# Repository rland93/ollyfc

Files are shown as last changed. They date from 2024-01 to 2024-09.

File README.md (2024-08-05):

# ollyfc
A small rust-embedded flight computer. RTIC, FrSky protocols, and STM32F4 hardware.

Board bring-up progress:

- [x] Buzzer
- [x] HDC 1080 Humidity and Temperature Sensor
- [x] BMI088 IMU
- [x] PCA9865 PWM Controller
- [x] Servo Channels from 5v power rail
- [x] FrSky SBUS External Reciever
- [x] BMP388 Pressure Sensor
- [x] LIS3MDL Magnetometer
- [x] FrSky SBUS 
- [ ] U-blox NEO m8n GPS unit
- [ ] NPA 730B differential pressure sensor
- [x] W25Q External Flash Memory
- [ ] UART for holybro 915MHz telemetry radio

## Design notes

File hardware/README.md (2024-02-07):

# OllyFC Hardware

We have hardware!

Schematics:

+ [V1 Schematic (PDF Link)](v1/ollyfc_v1_schematic.pdf)

# v1

V1 is manufactured by JLCPCB. The final project files (including JLCPCB Part Numbers / Bill of Materials) is in the v1/production folder. Images:

3D View (Tilted)

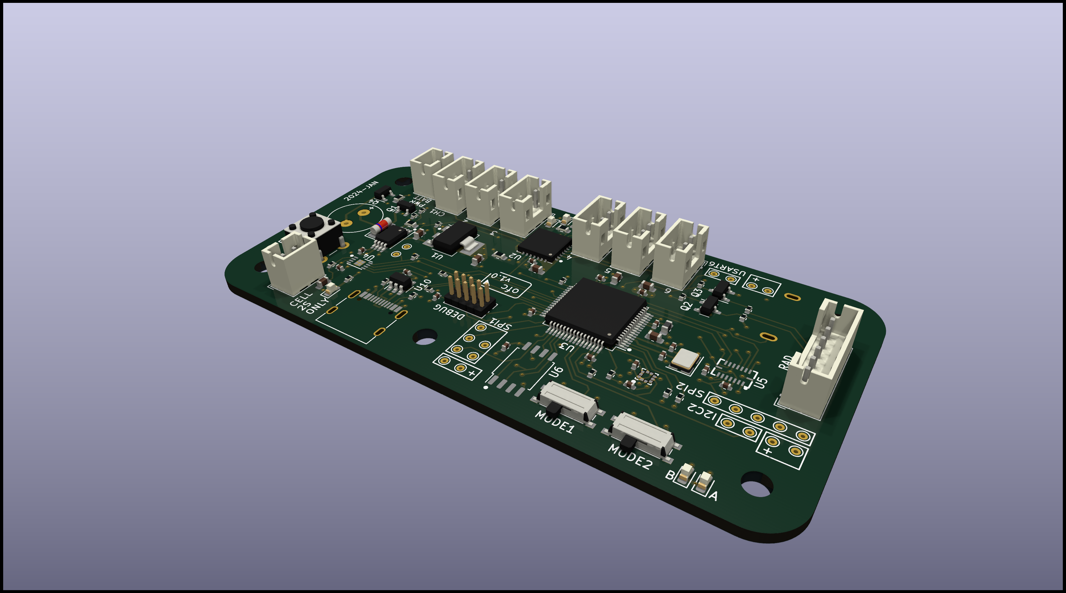
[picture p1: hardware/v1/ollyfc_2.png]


3D View (Top)

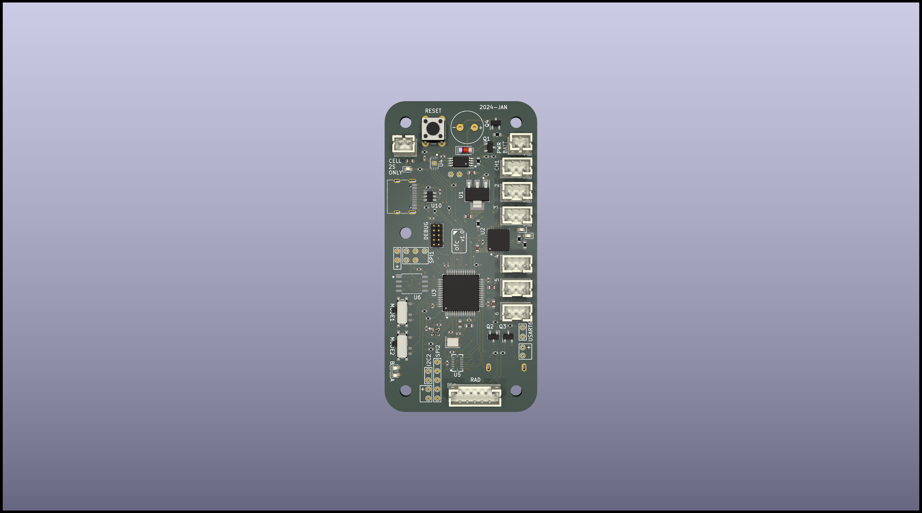
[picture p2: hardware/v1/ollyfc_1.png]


Traces (Top)

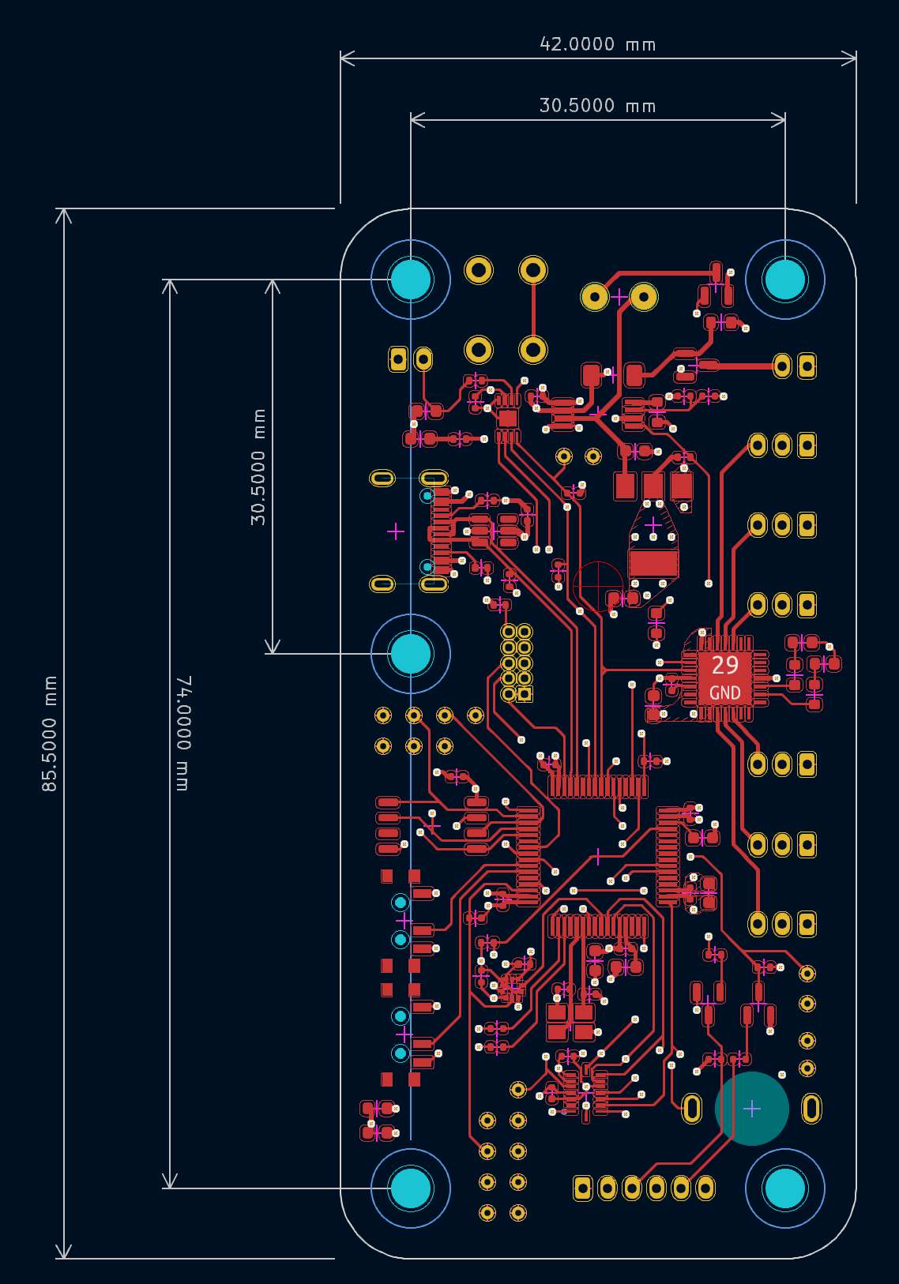
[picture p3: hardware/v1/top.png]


Traces (Bottom)

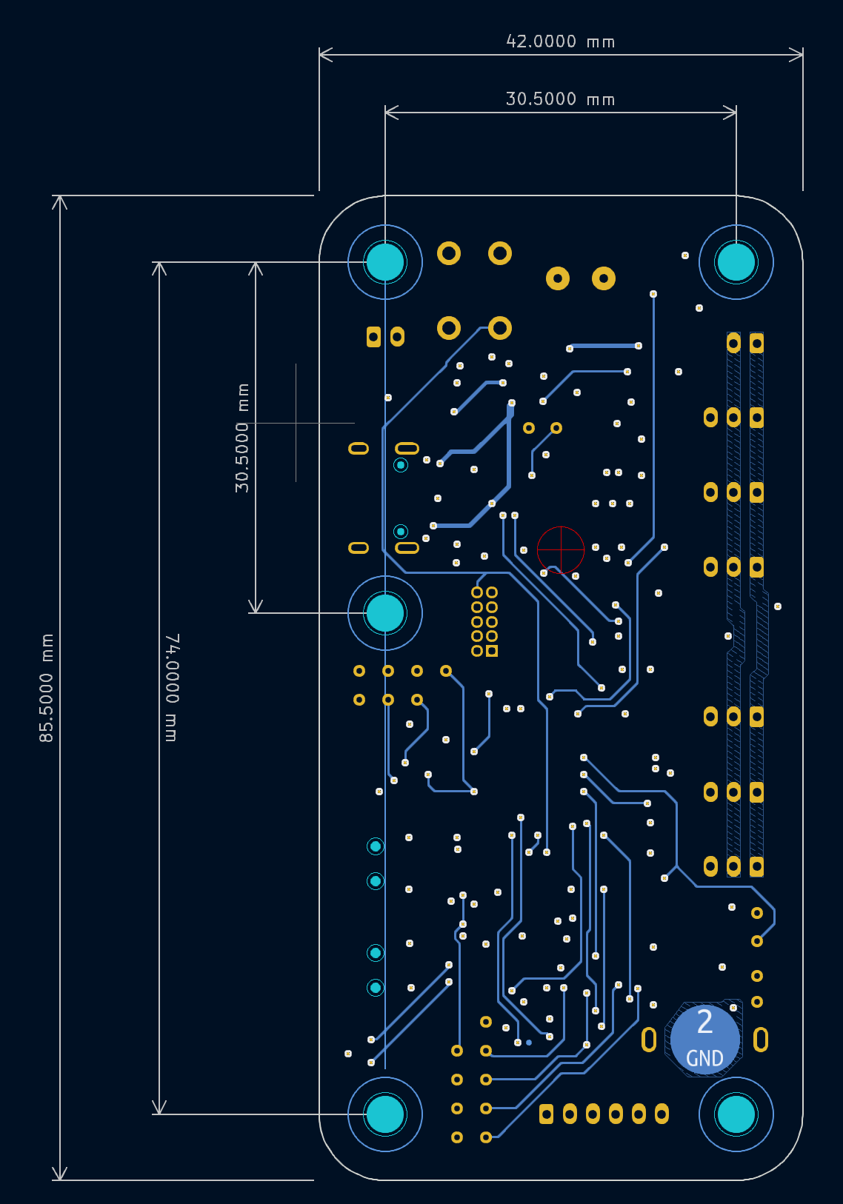
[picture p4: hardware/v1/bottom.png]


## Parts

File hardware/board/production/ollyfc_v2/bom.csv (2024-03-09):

Designator | Footprint | Quantity | Value | LCSC Part #
C1, C18, C19, C23, C7, C8 | 0603 | 6 | 4u7 | C19666
C10, C9 | 0402 | 2 | 12pF | C1547
C11, C12, C13, C14, C15, C16, C17, C2, C20, C21, C24, C25, C3, C4, C5, C6 | 0402 | 16 | 100n | C1525
C22 | 0402 | 1 | 1u | C52923
C26 | 0402 | 1 | 10n | C15195
CN1 | IDC-SMD_10P-P1.27_X1270WVS-2X05B-6TV01 | 1 | 20021521-00010T1LF | C2972785
D1, D2, D3, D4, D7 | LED0603-RD | 5 | KT-0603R | C2286
D5, D6 | LED0603-R-RD_WHITE | 2 | KT-0603W | C2290
D8 | SOT-23-6_L2.9-W1.6-P0.95-LS2.8-BL-1 | 1 | SRV05-4_C7420376 | C7420376
FB1 | 0603 | 1 | GZ1608D601TF | C1002
JP1 | RF-SMD_FRF05002-JSS103M | 1 | U.FL-R-SMT-1(80) | C88374
L1 | 0805 | 1 | 27nH | C98992
Q2, Q3, Q4 | SOT-23 | 3 | MMBT3904 | C20526
R1, R12, R15, R2, R21, R23, R25, R3, R4, R5, R8, R9 | 0402 | 12 | 5K1 | C25905
R10, R11, R16, R17, R20, R24, R6, R7 | 0402 | 8 | 1K5 | C25867
R13, R14, R22, R26 | 0603 | 4 | 680 | C23228
R19 | 0402 | 1 | 10 | C25077
TP1, TP10, TP11, TP12, TP13, TP14, TP15, TP16, TP17, TP18, TP19, TP2, TP20, TP21, TP22, TP23, TP24, TP3, TP3V3_0, TP3V3_1, TP3V3_2, TP3V3_3, TP4, TP6, TP7, TP8, TP9, TPG0, TPG1, TPG2, TPG3 | TestPoint_Pad_D1.5mm | 31 | TestPoint
U1 | SOT-223-3_L6.5-W3.4-P2.30-LS7.0-BR | 1 | AMS1117-3.3 | C6186
U10 | LGA-16_L4.5-W3.0-P0.50-BL | 1 | BMI088 | C194919
U2 | TSSOP-28_L9.7-W4.4-P0.65-LS6.4-TL | 1 | PCA9685PW,118 | C2678753
U3 | LQFP-64_10x10mm_P0.5mm | 1 | STM32F411RETx | C94355
U4 | SENSORM-SMD_BMP388 | 1 | BMP388 | C779278
U5 | LGA-12_L2.0-W2.0-P0.50-BL | 1 | LIS3MDLTR | C478483
U9 | SON-8_L3.0-W3.0-P0.65-LS3.0-BL-EP | 1 | TPS2113ADRBR | C354512
USB1 | USB-C_SMD-TYPE-C-31-M-12 | 1 | USB-TYPE-C-018 | C2927038
X1 | OSC-SMD_4P-L3.2-W2.5-BL | 1 | X322516MLB4SI | C13738

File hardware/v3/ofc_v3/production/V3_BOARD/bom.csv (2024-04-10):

Designator | Footprint | Quantity | Value | LCSC Part #
BT1 | BH-25C-1_ADM | 1 | 2998 | DNP
BZ1 | XDCR_CPT-3075-90T | 1 | 102-CPT-3075-90T-ND | DNP
C1, C11, C12, C13, C14, C15, C16, C19, C2, C20, C22, C23, C24, C27, C28, C29, C3, C30, C31, C32, C35, C36, C4, C5, C8, C9 | 0402 | 26 | 100n | C1525
C10, C21, C33 | 0402 | 3 | 4.7u | C23733
C17, C18 | 0603 | 2 | 4.7u | C19666
C25, C26 | 0402 | 2 | 33p | C1562
C34 | 0402 | 1 | 10n | C15195
C6, C7 | 0402 | 2 | 10p | C32949
CN1 | IDC-SMD_10P-P1.27_X1270WVS-2X05B-6TV01 | 1 | 20021521-00010T1LF | C2972785
CN2 | CONN-SMD_BM06B-SRSS-TBT-LF-SN | 1 | BM06B-SRSS-TBT(LF)(SN) | C495540
D1, D7 | 0603 | 2 | 19-213/Y2C-CQ2R2L/3T(CY) | C72038
D2, D4, D6 | 0603 | 3 | KT-0603R | C2286
D3 | SOT-23-6_L2.9-W1.6-P0.95-LS2.8-BL-1 | 1 | SRV05-4_C7420376 | C7420376
FB1 | 0603 | 1 | GZ1608D601TF | C1002
H1, H2, H3, H4, H5, H6 | MountingHole_3.2mm_M3 | 6 | DIN912 | DNP
J1 | JST_PH_B2B-PH-K_1x02_P2.00mm_Vertical | 1 | Conn_01x02 | DNP
J2, J3, J4 | PinHeader_1x08_P2.54mm_Vertical | 3 | Conn_01x09 | DNP
J5 | SMA-TH_KH-SMA-KE-Z | 1 | GNSS_RF | DNP
J6, J7 | JST_GH_SM06B-GHS-TB_1x06-1MP_P1.25mm_Horizontal | 2 | Conn_01x06 | C133065
J8 | PinHeader_1x03_P2.54mm_Vertical | 1 | Conn_01x03 | DNP
L1 | 0805 | 1 | 27nH | C98992
Q2, Q3 | SOT-23 | 2 | MMBT3904 | C20526
R1, R12, R13, R2, R25, R3, R4, R6 | 0402 | 8 | 5.1K | C25905
R10, R11, R21 | 0402 | 3 | 1K | C11702
R14, R15, R16, R17 | 0402 | 4 | 5.1K | C25905
R18, R19 | 0402 | 2 | 1.5K | C25867
R20 | 0603 | 1 | 3K | C4211
R22 | 0603 | 1 | 10 | C22859
R23 | 0603 | 1 | 7.5K | C23234
R24, R26, R27, R5, R9 | 0603 | 5 | 150 | C22808
R7, R8 | 0402 | 2 | 1.5K | C25867
SW1, SW2 | SW_PUSH_1P1T_6x3.5mm_H4.3_APEM_MJTP1243 | 2 | SW_RST | DNP
TP1, TP10, TP11, TP12, TP13, TP14, TP15, TP16, TP17, TP18, TP19, TP20, TP21, TP22, TP23, TP24, TP25, TP26, TP27, TP28, TP29, TP30, TP31, TP32, TP33, TP34, TP35, TP36, TP37, TP38, TP39, TP4, TP40, TP41, TP42, TP43, TP5, TP6, TP7, TP8, TP9 | TestPoint_Pad_D1.0mm | 41 | TestPoint
TP2, TP3 | TestPoint_Pad_2.0x2.0mm | 2 | TestPoint | DNP
U1 | LQFP-64_10x10mm_P0.5mm | 1 | STM32F401RCTx | C74524
U10 | Texas_PWSON-N6 | 1 | HDC1080 | C82227
U11 | LGA-12_2x2mm_P0.5mm | 1 | LIS3MDL | C478483
U12 | ublox_NEO | 1 | NEO-M8N | DNP
U2 | SENSORM-SMD_BMP388 | 1 | BMP388 | C779278
U3 | LGA-16_L4.5-W3.0-P0.50-BL | 1 | BMI088 | C194919
U4 | USB-C-SMD_G-SWITCH_GT-USB-7010ASV | 1 | GT-USB-7010ASV | C2988369
U5 | SOIC-14W_7.5x9mm_P1.27mm | 1 | NPA-730B-10WD | DNP
U6 | SOT-223 | 1 | AMS1117-3.3 | C6186
U7 | VSON-8-1EP_3x3mm_P0.65mm_EP1.65x2.4mm | 1 | TPS2113ADRBR | C354512
U8 | TSSOP-28_4.4x9.7mm_P0.65mm | 1 | PCA9685PW | C2678753
U9 | SOIC-8_5.23x5.23mm_P1.27mm | 1 | W25Q128JVS | DNP
X1 | OSC-SMD_4P-L3.2-W2.5-BL | 1 | X322512MSB4SI | C9002
X2 | FC-135R_L3.2-W1.5 | 1 | Q13FC1350000400 | C32346

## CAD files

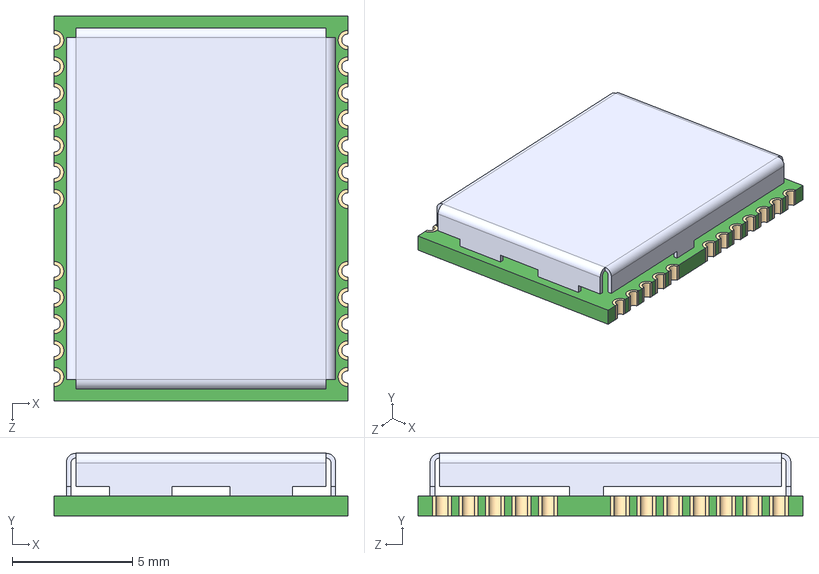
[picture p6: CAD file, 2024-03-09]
hardware/board/NEO-M9N-00B.step
12.2 x 2.60 x 16.0 mm

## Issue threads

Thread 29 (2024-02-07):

Pin Remap

rland93, 2024-02-07:
Pins are configured to the prototype PCB. They need to be remapped to the hardware.

rland93, 2024-08-05:
marking this done as v3 has standard pinout now

Closed 2024-08-05.

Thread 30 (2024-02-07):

BMI088 Driver

rland93, 2024-02-07:
Hardware was updated to use BMI088, not the BMI160. So we need to either write or bring in a driver for it.

- [x] create bbu-bmi088 example for testing with skeleton for reading data
- [x] bring in bmi088-rs crate
- [x] set up i2c pins and device
- [x] read chipid

Closed 2024-08-20.

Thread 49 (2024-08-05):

wishlist for next board rev

rland93, 2024-08-05:
I probably won't do another rev for quite some time, but this is my tracking wishlist so far.

- smaller and lighter buzzer
- remove or reduce filtering on the buzzer
- better frequency analysis for the buzzer in general...
- JST-GH-6P connectors for everything. pixhawk uses them; frsky uses them; holybro radio uses them. they should be standard for various things that you might attach
- a flatter RTC battery connector, the one we have is cheap/bulky/weighty/not flat
- larger resistor for the always-on USB / battery lights. they are too bright and it's tough to see the indicators when connected and probably eat too much power
- better test points. maybe just do a 2.54mm header on one side of the board? with jumpers to enable/disable stuff? then test board can be a HAT. idk. the test points we have require a pogo fixture which is not _bad_ but also not really ideal for the small-scale prototyping we are doing and the types of hacking an end user might do in the field (e.g. connecting a Pi or other sensors).

stretch, probably not possible:

- would love to reduce the size of the board. I think it can be done especially with a smaller buzzer and moving some larger SMT components (all power stuff?) to the opposite side of the board.
- nordic nrf5810 BLE chip.
- stm32h series instead of the f4. 64k is dinky.

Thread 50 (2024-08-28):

Set up SPI communication with flash

rland93, 2024-08-28:
[x] Find or write driver
[x] Create validation example for reading writing pages and erasing blocks
[x] Test & validate example
[ ] DMA

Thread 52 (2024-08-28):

Log Entry Structure

rland93, 2024-08-28:
- Tagged union. Members have serde traits
- Add 3-4 common data types. e.g. raw imu sensor data frame, rx frame, some data types for the i2c sensors
- Include log levels (debug, common, warnings) in metadata
- Include timestamps in metadata

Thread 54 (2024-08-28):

Generic RTIC logging task

rland93, 2024-08-28:
somehow it should be possible to have extern RTIC tasks that we can create using embedded-hal traits.

I'd like a pair of tasks:

- write task that coordinates with the driver to drain the queue. use the driver traits.
- double buffered dma task that handles the driver initiating a write op when driver indicates that it is ready to write
- write init takes semaphore
- dma interrupt releases semaphore

ideally these tasks and interrupts are constructed using embedded-hal dma, Flash traits from #51, and a generic queue #53.

such that write and the ISR can be easily imported in the main application.

validation in an example application.

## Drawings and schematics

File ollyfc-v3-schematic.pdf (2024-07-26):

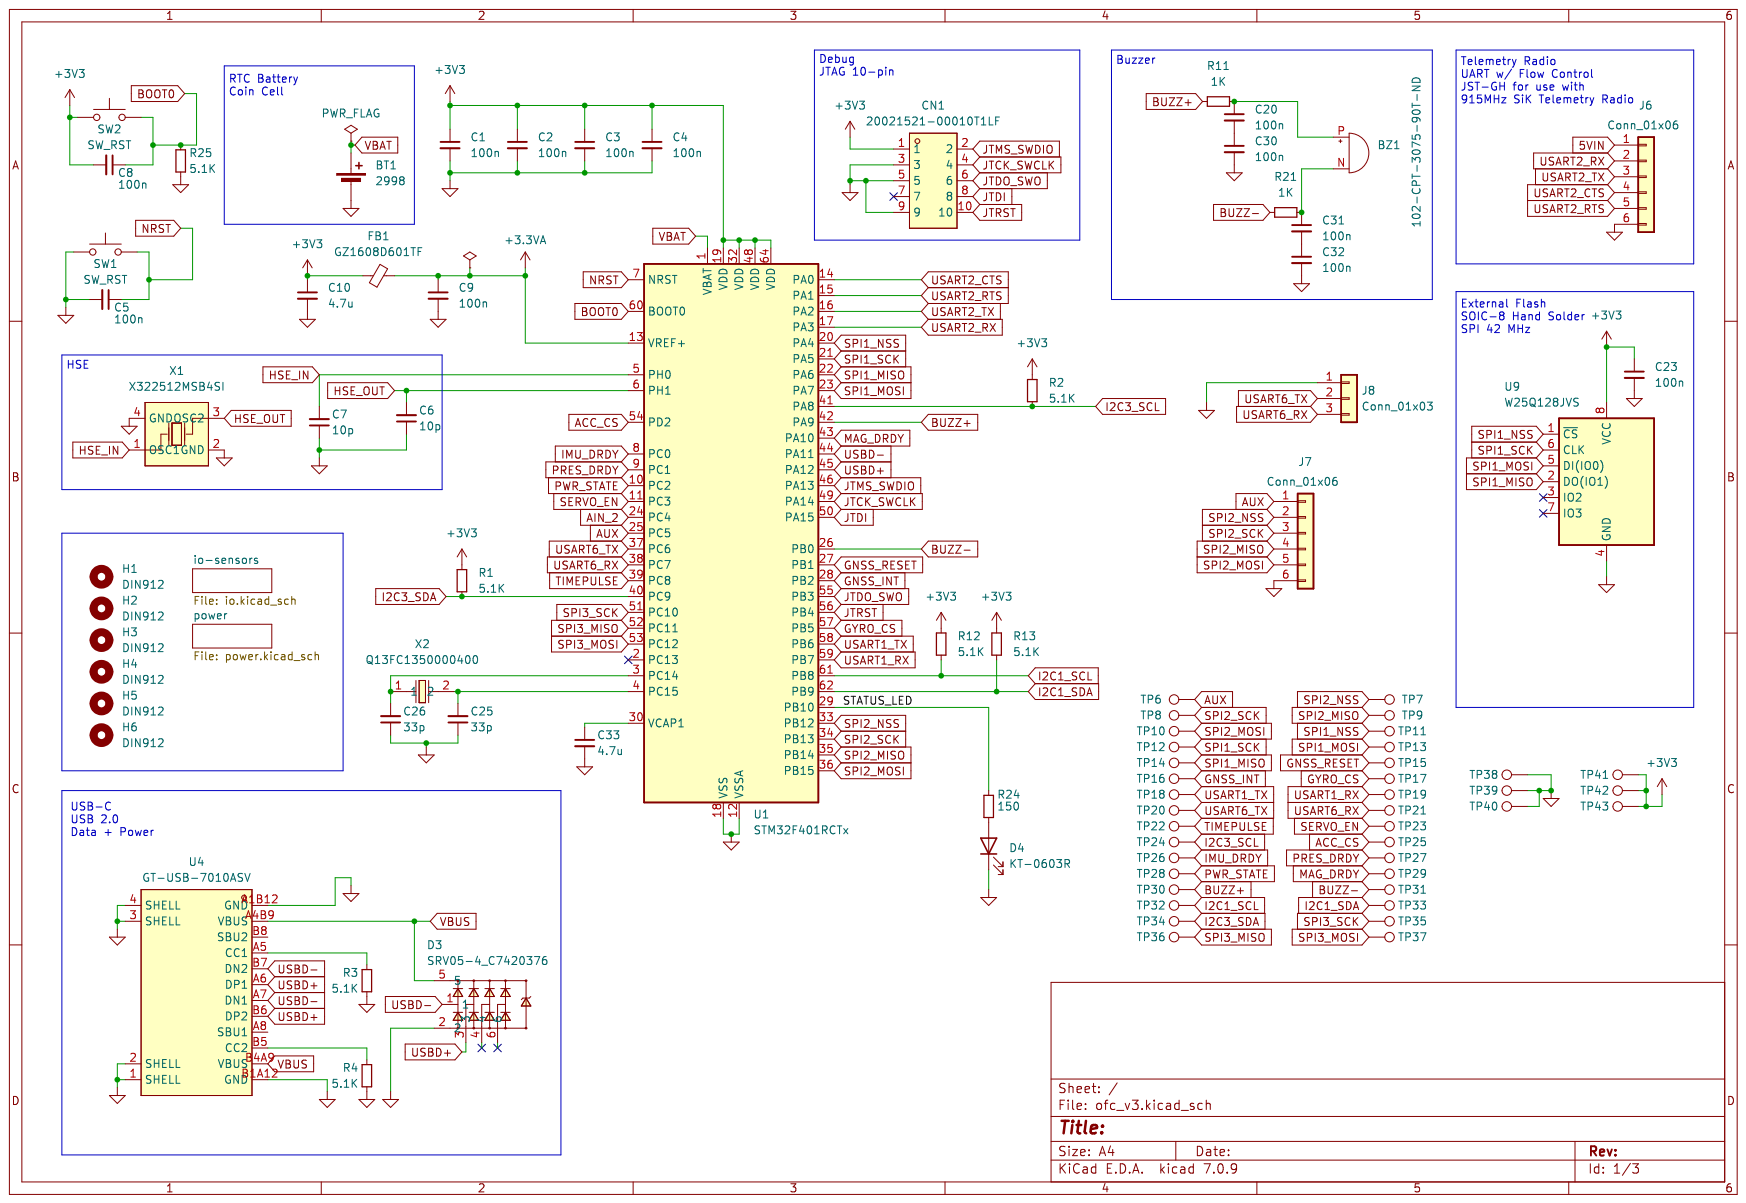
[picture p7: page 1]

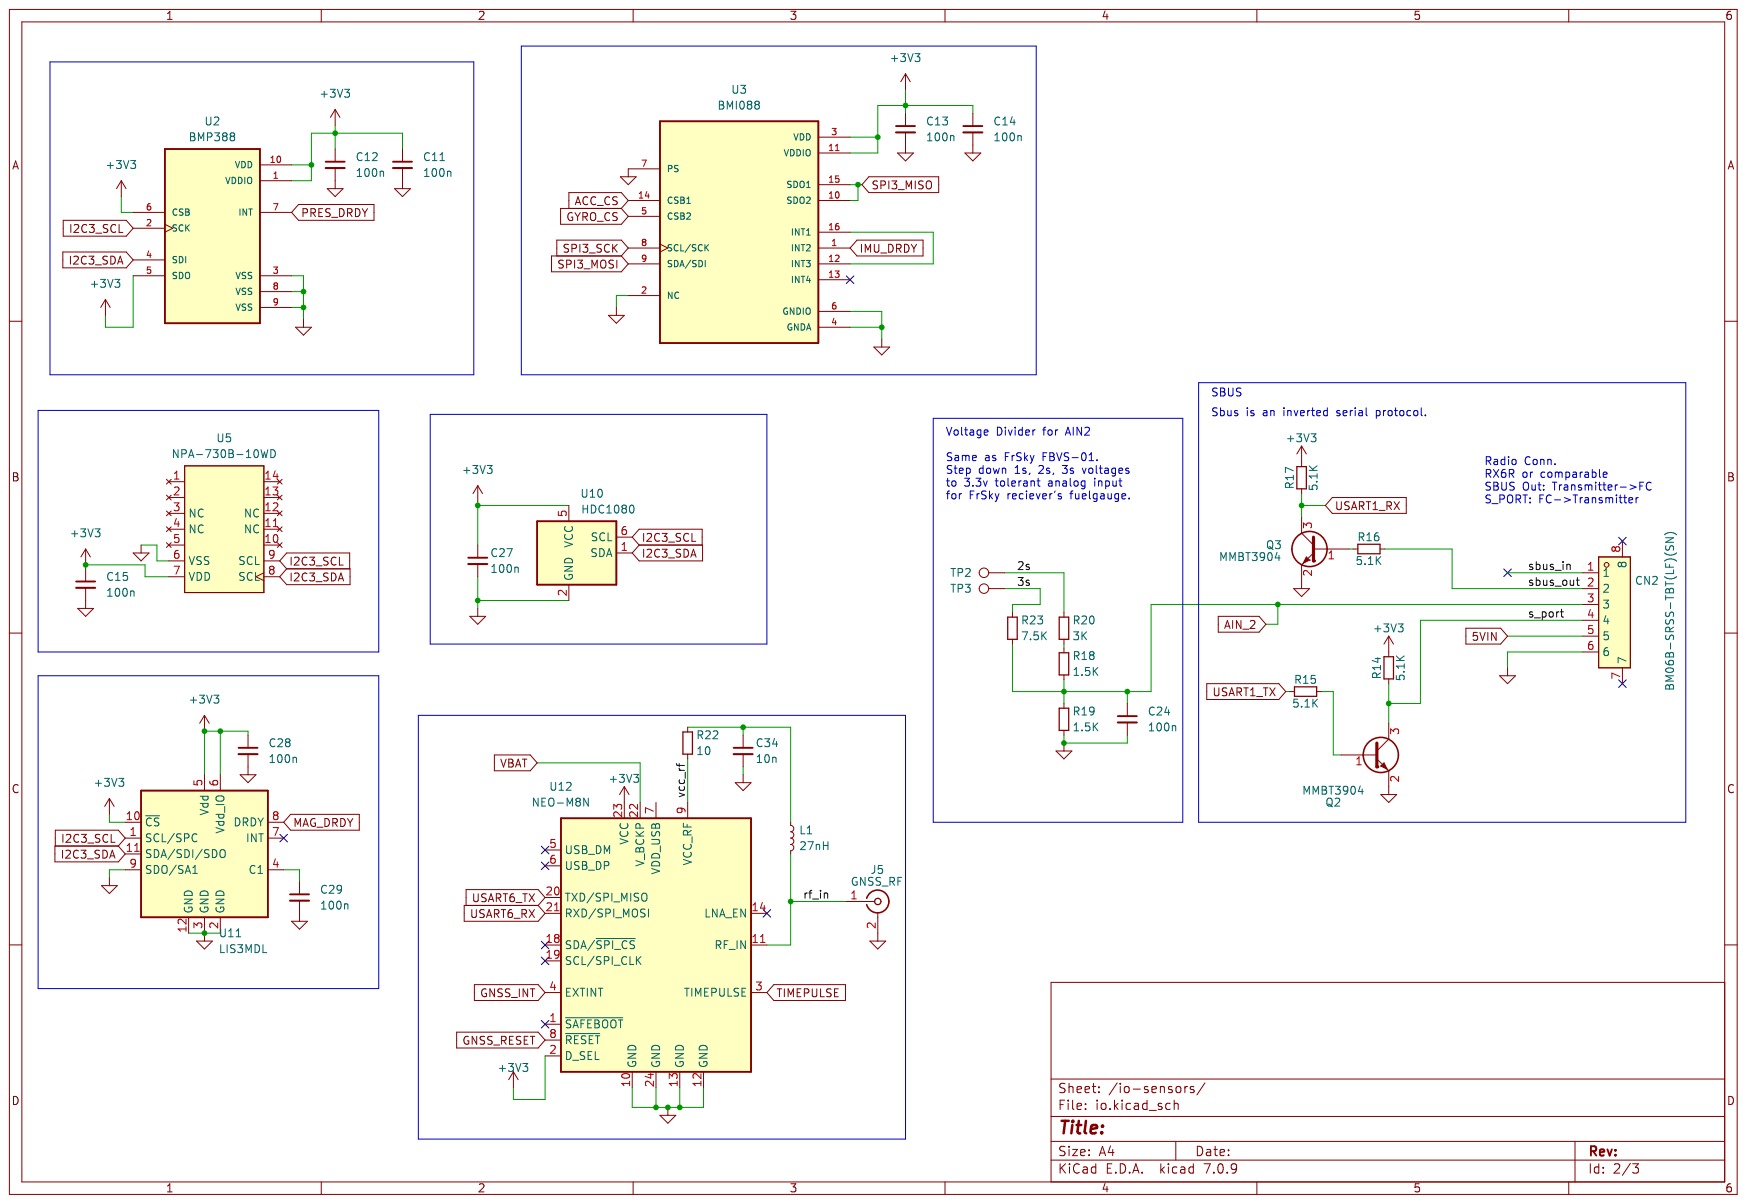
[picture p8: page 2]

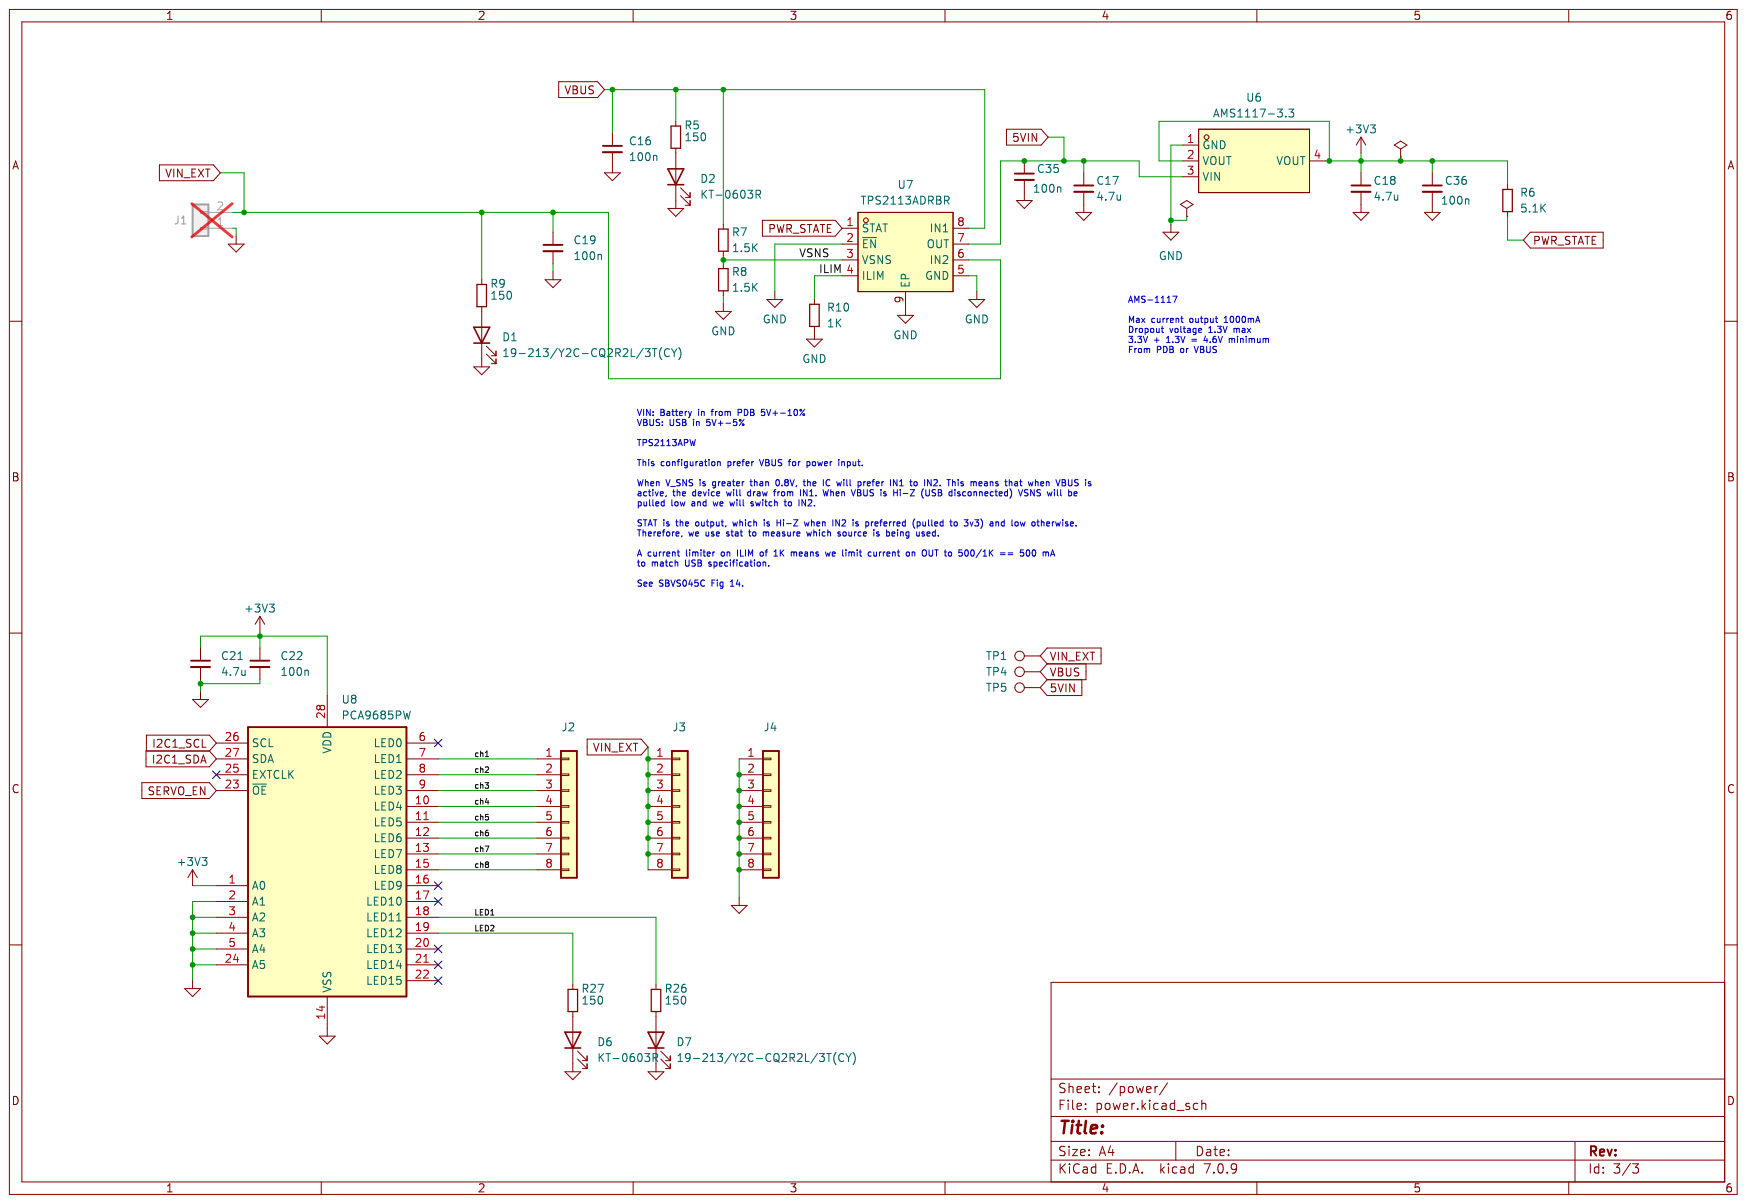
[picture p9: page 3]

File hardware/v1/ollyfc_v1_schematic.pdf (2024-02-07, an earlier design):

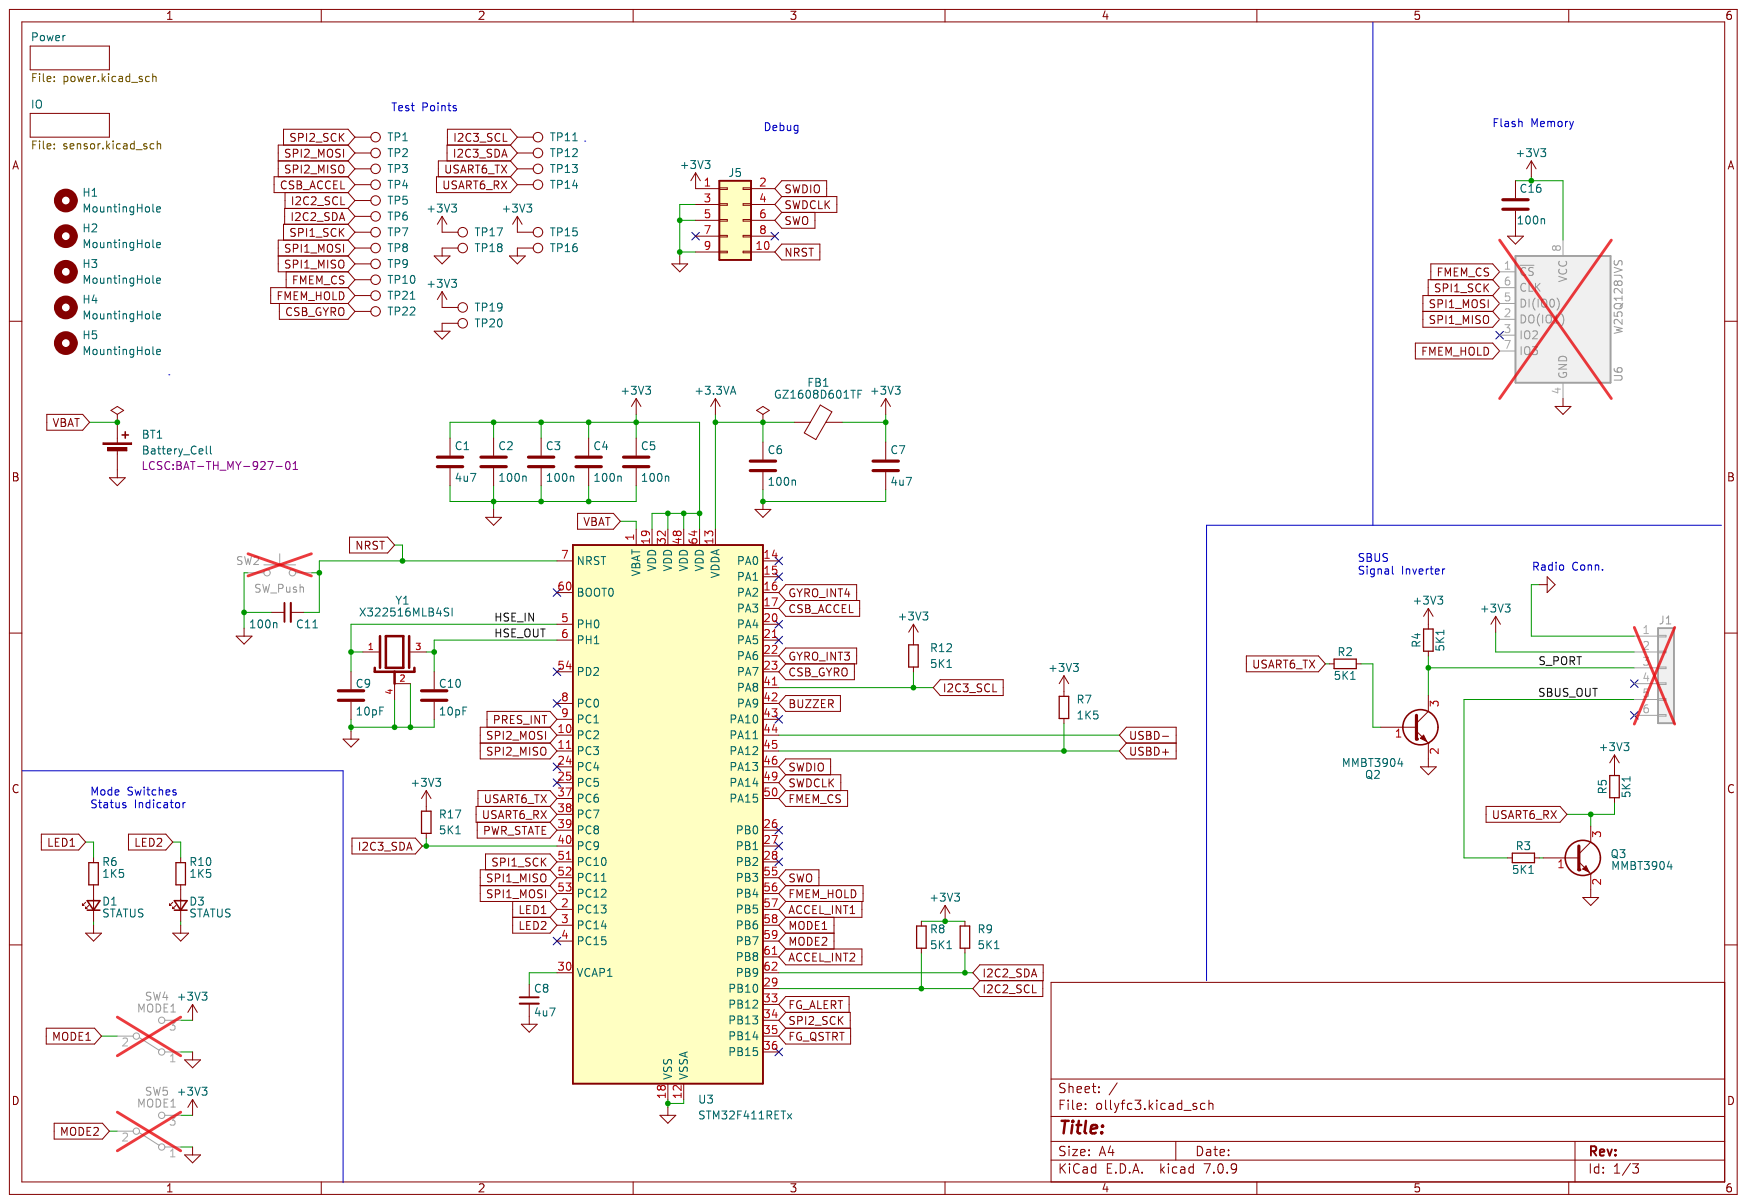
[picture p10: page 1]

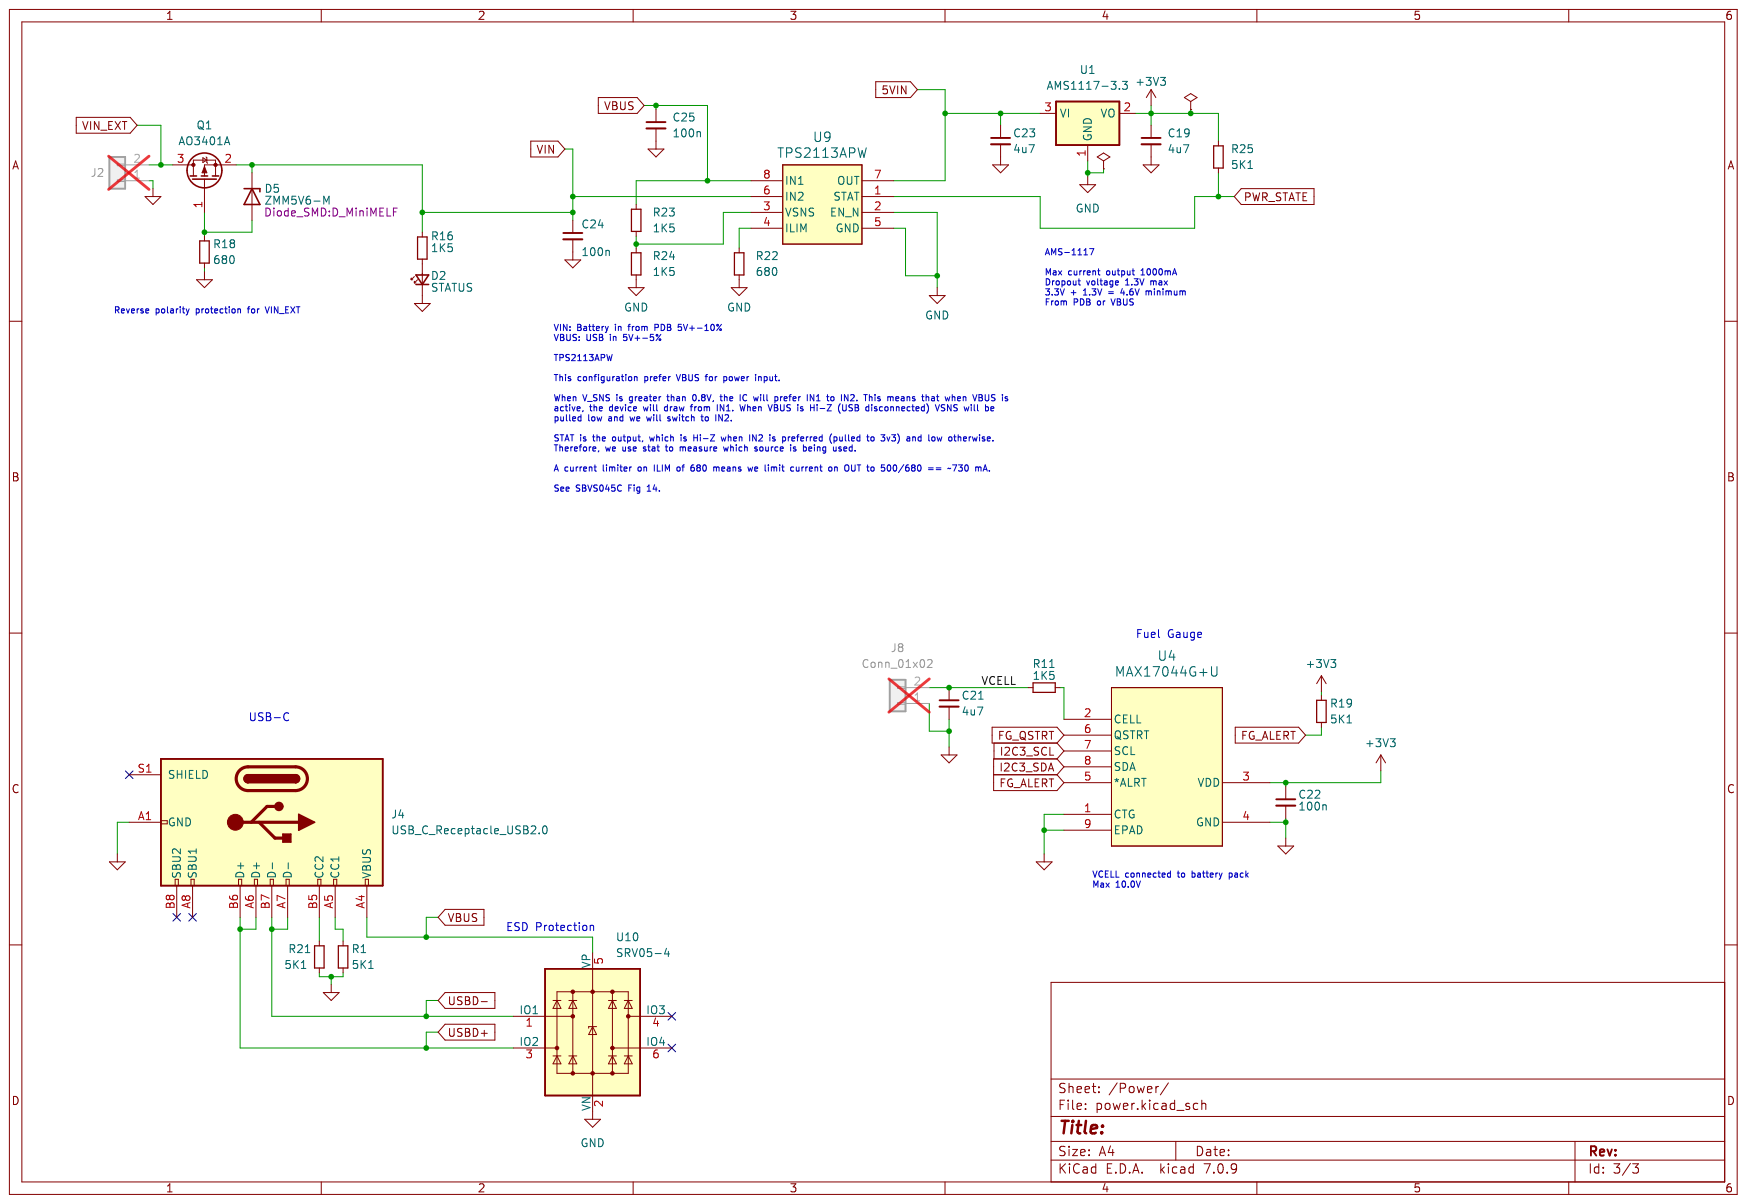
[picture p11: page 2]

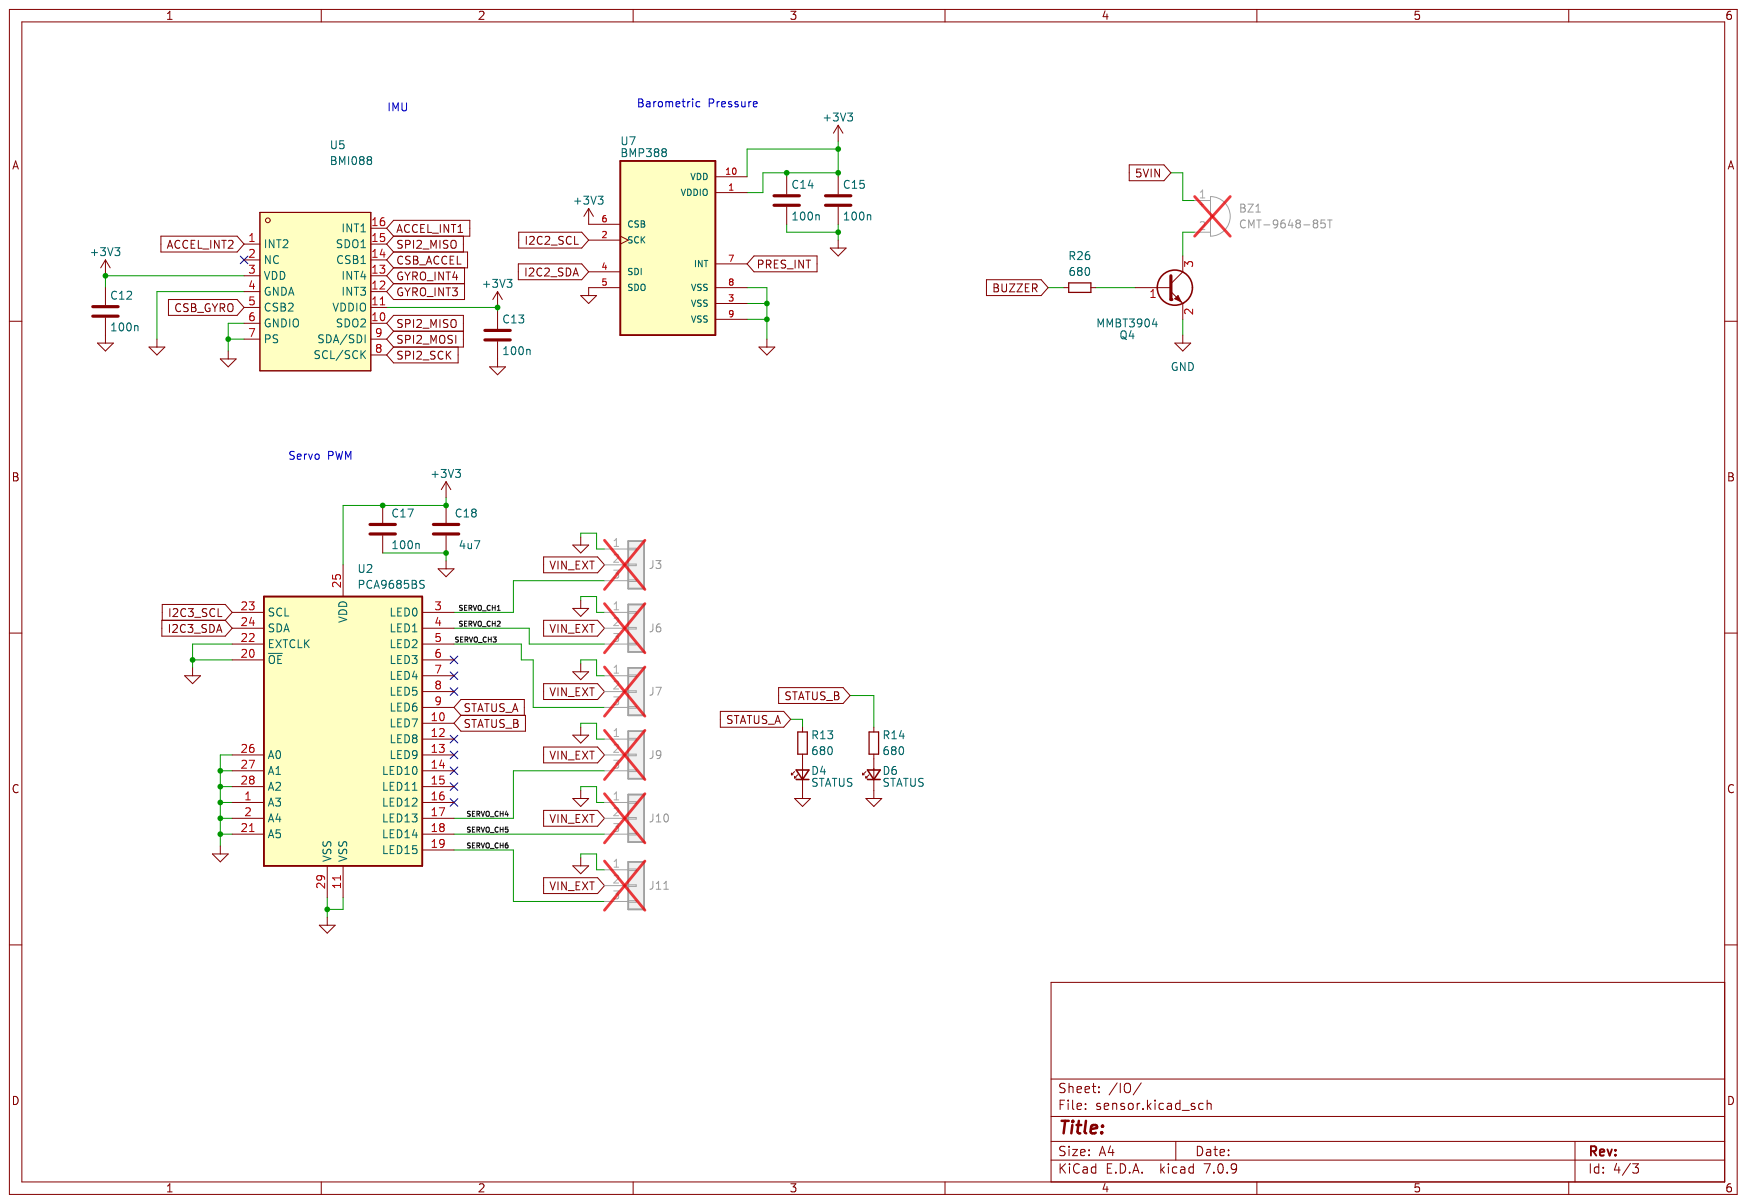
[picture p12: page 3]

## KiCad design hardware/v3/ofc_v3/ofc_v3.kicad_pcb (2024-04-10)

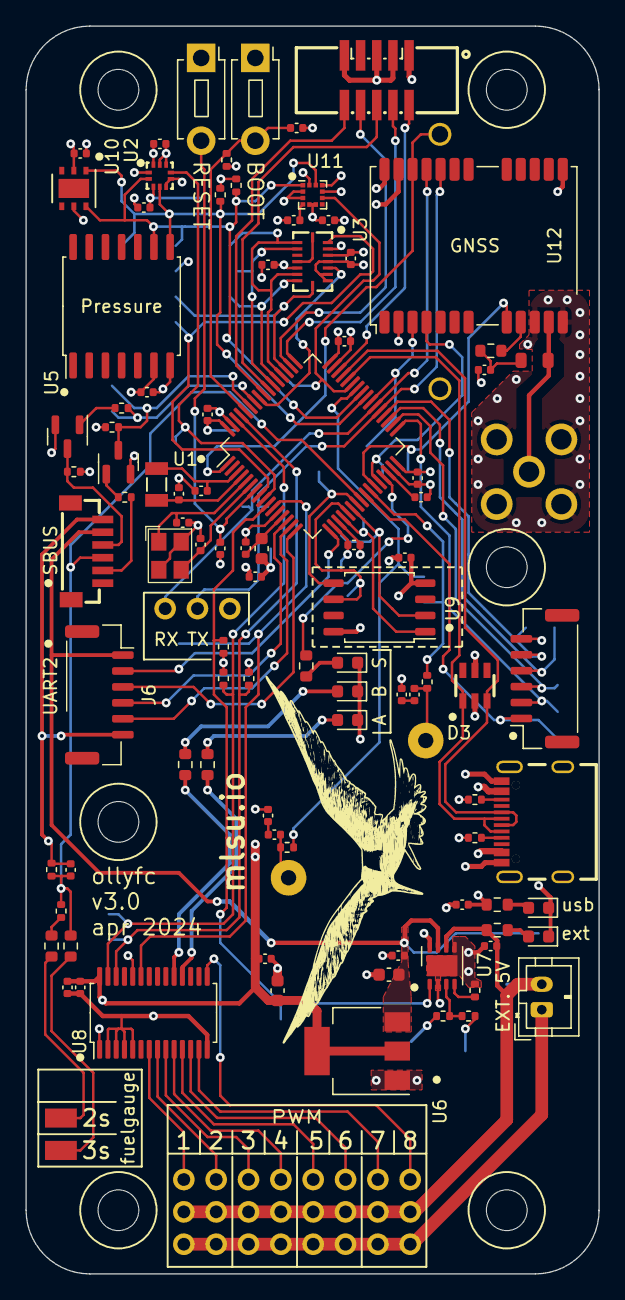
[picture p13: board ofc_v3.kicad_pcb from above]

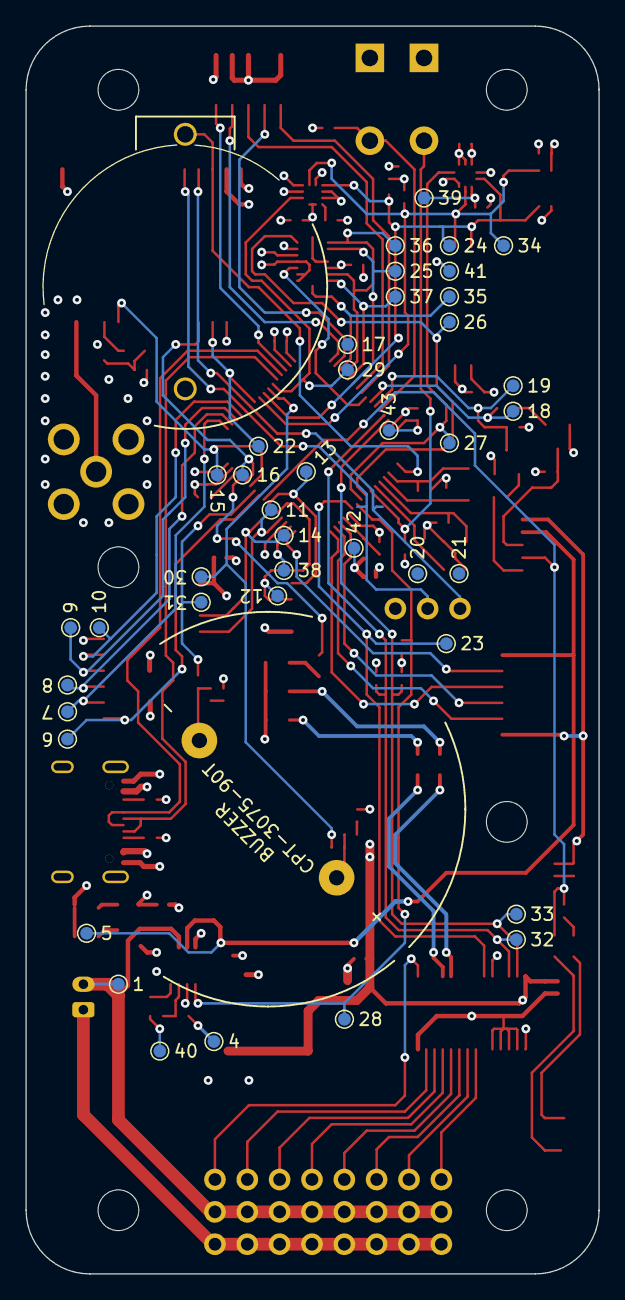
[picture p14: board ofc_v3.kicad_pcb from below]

Board: 4 copper layers, 45.0 x 98.0 mm, 150 parts (43 on the bottom side), 94 nets.

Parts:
BT1: 2998; BH-25C-1_ADM
BZ1: 102-CPT-3075-90T-ND; XDCR_CPT-3075-90T
C1, C2, C3, C4, C5, C8, C9, C11, C12, C13, C14, C15, C16, C19, C20, C22, C23, C24, C27, C28, C29, C30, C31, C32, C35, C36: 100n; C_0402_1005Metric
C6, C7: 10p; C_0402_1005Metric
C10, C21, C33: 4.7u; C_0402_1005Metric
C17, C18: 4.7u; C_0603_1608Metric
C25, C26: 33p; C_0402_1005Metric
C34: 10n; C_0402_1005Metric
CN1: 20021521-00010T1LF; IDC-SMD_10P-P1.27_X1270WVS-2X05B-6TV01
CN2: BM06B-SRSS-TBT(LF)(SN); CONN-SMD_BM06B-SRSS-TBT-LF-SN
D1, D7: 19-213/Y2C-CQ2R2L/3T(CY); LED_0603_1608Metric
D2, D4, D6: KT-0603R; LED_0603_1608Metric
D3: SRV05-4_C7420376; SOT-23-6_L2.9-W1.6-P0.95-LS2.8-BL-1
FB1: GZ1608D601TF; L_0603_1608Metric
H1, H2, H3, H4, H5, H6: DIN912; MountingHole_3.2mm_M3
J1: Conn_01x02; JST_PH_B2B-PH-K_1x02_P2.00mm_Vertical
J2, J3, J4: Conn_01x09; PinHeader_1x08_P2.54mm_Vertical
J5: GNSS_RF; SMA-TH_KH-SMA-KE-Z
J6, J7: Conn_01x06; JST_GH_SM06B-GHS-TB_1x06-1MP_P1.25mm_Horizontal
J8: Conn_01x03; PinHeader_1x03_P2.54mm_Vertical
L1: 27nH; L_0805_2012Metric
Q2, Q3: MMBT3904; SOT-23
R1, R2, R3, R4, R6, R12, R13, R14, R15, R16, R17, R25: 5.1K; R_0402_1005Metric
R5, R9, R24, R26, R27: 150; R_0603_1608Metric
R7, R8, R18, R19: 1.5K; R_0402_1005Metric
R10, R11, R21: 1K; R_0402_1005Metric
R20: 3K; R_0603_1608Metric
R22: 10; R_0603_1608Metric
R23: 7.5K; R_0603_1608Metric
SW1, SW2: SW_RST; SW_PUSH_1P1T_6x3.5mm_H4.3_APEM_MJTP1243
TP1, TP4, TP5, TP6, TP7, TP8, TP9, TP10, TP11, TP12, TP13, TP14, TP15, TP16, TP17, TP18, TP19, TP20, TP21, TP22, TP23, TP24, TP25, TP26, TP27, TP28, TP29, TP30, TP31, TP32, TP33, TP34, TP35, TP36, TP37, TP38, TP39, TP40, TP41, TP42, TP43: TestPoint; TestPoint_Pad_D1.0mm
TP2, TP3: TestPoint; TestPoint_Pad_2.0x2.0mm
U1: STM32F401RCTx; LQFP-64_10x10mm_P0.5mm
U2: BMP388; SENSORM-SMD_BMP388
U3: BMI088; LGA-16_L4.5-W3.0-P0.50-BL
U4: GT-USB-7010ASV; USB-C-SMD_G-SWITCH_GT-USB-7010ASV
U5: NPA-730B-10WD; SOIC-14W_7.5x9mm_P1.27mm
U6: AMS1117-3.3; SOT-223
U7: TPS2113ADRBR; VSON-8-1EP_3x3mm_P0.65mm_EP1.65x2.4mm
U8: PCA9685PW; TSSOP-28_4.4x9.7mm_P0.65mm
U9: W25Q128JVS; SOIC-8_5.23x5.23mm_P1.27mm
U10: HDC1080; Texas_PWSON-N6
U11: LIS3MDL; LGA-12_2x2mm_P0.5mm
U12: NEO-M8N; ublox_NEO
X1: X322512MSB4SI; OSC-SMD_4P-L3.2-W2.5-BL
X2: Q13FC1350000400; FC-135R_L3.2-W1.5

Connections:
5VIN: C17.1, C35.1, CN2.5, J6.1, TP5.1, U6.3 (VIN), U7.7 (OUT)
+3.3VA: C9.1, FB1.2, U1.13 (VREF+)
+3V3: C1.1, C2.1, C3.1, C4.1, C8.2, C10.1, C11.1, C12.1, C13.1, C14.1, C15.1, C18.1, C21.1, C22.1, C23.1, C27.1, C28.1, C36.1, CN1.1, FB1.1, R1.2, R2.2, R6.1, R12.2, R13.2, R14.2, R17.2, SW2.1, TP41.1, TP42.1, TP43.1, U1.19 (VDD), U1.32 (VDD), U1.48 (VDD), U1.64 (VDD), U2.1 (VDDIO), U2.5 (SDO), U2.6 (CSB), U2.10 (VDD), U3.3 (VDD), U3.11 (VDDIO), U5.7 (VDD), U6.2 (VOUT), U6.4 (VOUT), U8.1 (A0), U8.28 (VDD), U9.8 (VCC), U10.5 (VCC), U11.5 (Vdd), U11.6 (Vdd_IO), U11.10 (~CS), U12.2 (D_SEL), U12.23 (VCC)
/STATUS_LED: R24.1, U1.29 (PB10)
/io-sensors/2s: R20.1, TP2.1
/io-sensors/3s: R23.1, TP3.1
/io-sensors/rf_in: J5.1 (In), L1.2, U12.11 (RF_IN)
/io-sensors/s_port: CN2.4, Q2.3 (C), R14.1
/io-sensors/sbus_out: CN2.2, R16.2
/io-sensors/vcc_rf: R22.2, U12.9 (VCC_RF)
/power/ILIM: R10.1, U7.4 (ILIM)
/power/LED1: R26.1, U8.18 (LED11)
/power/LED2: R27.1, U8.19 (LED12)
/power/VSNS: R7.2, R8.1, U7.3 (VSNS)
/power/ch1: J2.1, U8.7 (LED1)
/power/ch2: J2.2, U8.8 (LED2)
/power/ch3: J2.3, U8.9 (LED3)
/power/ch4: J2.4, U8.10 (LED4)
/power/ch5: J2.5, U8.11 (LED5)
/power/ch6: J2.6, U8.12 (LED6)
/power/ch7: J2.7, U8.13 (LED7)
/power/ch8: J2.8, U8.15 (LED8)
ACC_CS: TP25.1, U1.54 (PD2), U3.14 (CSB1)
AIN_2: C24.1, CN2.3, R18.2, R19.1, R23.2, U1.24 (PC4)
AUX: J7.1, TP6.1, U1.25 (PC5)
BOOT0: C8.1, R25.2, SW2.2, U1.60 (BOOT0)
BUZZ+: R11.1, TP30.1, U1.42 (PA9)
BUZZ-: R21.1, TP31.1, U1.26 (PB0)
GND: BT1.2 (-), C1.2, C2.2, C3.2, C4.2, C5.2, C6.1, C7.1, C9.2, C10.2, C11.2, C12.2, C13.2, C14.2, C15.2, C16.2, C17.2, C18.2, C19.2, C21.2, C22.2, C23.2, C24.2, C25.1, C26.1, C27.2, C28.2, C29.2, C30.2, C32.2, C33.2, C34.2, C35.2, C36.2, CN1.3, CN1.5, CN1.9, CN2.6, D1.1 (K), D2.1 (K), D3.2, D4.1 (K), D6.1 (K), D7.1 (K), J1.1, J4.1, J4.2, J4.3, J4.4, J4.5, J4.6, J4.7, J4.8, J5.2 (Ext), J6.6, J7.6, J8.1, Q2.2 (E), Q3.2 (E), R3.1, R4.1, R8.2, R10.2, R19.2, R25.1, SW1.1, TP38.1, TP39.1, TP40.1, U1.12 (VSSA), U1.18 (VSS), U1.31 (VSS), U1.47 (VSS), U1.63 (VSS), U2.3 (VSS), U2.8 (VSS), U2.9 (VSS), U3.2 (NC), U3.4 (GNDA), U3.6 (GNDIO), U3.7 (PS), U4.1 (SHELL), U4.2 (SHELL), U4.3 (SHELL), U4.4 (SHELL), U4.A1B12 (GND), U4.B1A12 (GND), U5.6 (VSS), U6.1 (GND), U7.2 (~EN), U7.5 (GND), U7.9 (EP), U8.2 (A1), U8.3 (A2), U8.4 (A3), U8.5 (A4), U8.14 (VSS), U8.24 (A5), U9.4 (GND), U10.2 (GND), U11.2 (GND), U11.3 (GND), U11.9 (SDO/SA1), U11.12 (GND), U12.10 (GND), U12.12 (GND), U12.13 (GND), U12.24 (GND), X1.2 (GND), X1.4 (GND)
GNSS_INT: TP16.1, U1.28 (PB2), U12.4 (EXTINT)
GNSS_RESET: TP15.1, U1.27 (PB1), U12.8 (~RESET)
GYRO_CS: TP17.1, U1.57 (PB5), U3.5 (CSB2)
HSE_IN: C7.2, U1.5 (PH0), X1.1 (OSC1)
HSE_OUT: C6.2, U1.6 (PH1), X1.3 (OSC2)
I2C1_SCL: R12.1, TP32.1, U1.61 (PB8), U8.26 (SCL)
I2C1_SDA: R13.1, TP33.1, U1.62 (PB9), U8.27 (SDA)
I2C3_SCL: R2.1, TP24.1, U1.41 (PA8), U2.2 (SCK), U5.9 (SCL), U10.6 (SCL), U11.1 (SCL/SPC)
I2C3_SDA: R1.1, TP34.1, U1.40 (PC9), U2.4 (SDI), U5.8 (SCL), U10.1 (SDA), U11.11 (SDA/SDI/SDO)
IMU_DRDY: TP26.1, U1.8 (PC0), U3.1 (INT2)
JTCK_SWCLK: CN1.4, U1.49 (PA14)
JTDI: CN1.8, U1.50 (PA15)
JTDO_SWO: CN1.6, U1.55 (PB3)
JTMS_SWDIO: CN1.2, U1.46 (PA13)
JTRST: CN1.10, U1.56 (PB4)
MAG_DRDY: TP29.1, U1.43 (PA10), U11.8 (DRDY)
NRST: C5.1, SW1.2, U1.7 (NRST)
unnamed: BZ1.N, C31.1, R21.2
unnamed: BZ1.P, C20.1, R11.2
unnamed: C20.2, C30.1
unnamed: C31.2, C32.1
unnamed: C34.1, L1.1, R22.1
unnamed: D1.2 (A), R9.2
unnamed: D2.2 (A), R5.2
unnamed: D4.2 (A), R24.2
unnamed: D6.2 (A), R27.2
unnamed: D7.2 (A), R26.2
unnamed: Q2.1 (B), R15.2
unnamed: Q3.1 (B), R16.1
unnamed: R18.1, R20.2
unnamed: C26.2, U1.3 (PC14), X2.1
unnamed: C25.2, U1.4 (PC15), X2.2
unnamed: C33.1, U1.30 (VCAP1)
unnamed: U3.12 (INT3), U3.16 (INT1)
unnamed: R3.2, U4.A5 (CC1)
unnamed: R4.2, U4.B5 (CC2)
unnamed: C29.1, U11.4 (C1)
PRES_DRDY: TP27.1, U1.9 (PC1), U2.7 (INT)
PWR_STATE: R6.2, TP28.1, U1.10 (PC2), U7.1 (STAT)
SERVO_EN: TP23.1, U1.11 (PC3), U8.23 (~OE)
SPI1_MISO: TP14.1, U1.22 (PA6), U9.2 (DO(IO1))
SPI1_MOSI: TP13.1, U1.23 (PA7), U9.5 (DI(IO0))
SPI1_NSS: TP11.1, U1.20 (PA4), U9.1 (~CS)
SPI1_SCK: TP12.1, U1.21 (PA5), U9.6 (CLK)
SPI2_MISO: J7.4, TP9.1, U1.35 (PB14)
SPI2_MOSI: J7.5, TP10.1, U1.36 (PB15)
SPI2_NSS: J7.2, TP7.1, U1.33 (PB12)
SPI2_SCK: J7.3, TP8.1, U1.34 (PB13)
SPI3_MISO: TP36.1, U1.52 (PC11), U3.10 (SDO2), U3.15 (SDO1)
SPI3_MOSI: TP37.1, U1.53 (PC12), U3.9 (SDA/SDI)
SPI3_SCK: TP35.1, U1.51 (PC10), U3.8 (SCL/SCK)
TIMEPULSE: TP22.1, U1.39 (PC8), U12.3 (TIMEPULSE)
USART1_RX: Q3.3 (C), R17.1, TP19.1, U1.59 (PB7)
USART1_TX: R15.1, TP18.1, U1.58 (PB6)
USART2_CTS: J6.4, U1.14 (PA0)
USART2_RTS: J6.5, U1.15 (PA1)
USART2_RX: J6.2, U1.17 (PA3)
USART2_TX: J6.3, U1.16 (PA2)
USART6_RX: J8.3, TP21.1, U1.38 (PC7), U12.21 (RXD/SPI_MOSI)
USART6_TX: J8.2, TP20.1, U1.37 (PC6), U12.20 (TXD/SPI_MISO)
USBD+: D3.3, U1.45 (PA12), U4.A6 (DP1), U4.B6 (DP2)
USBD-: D3.1, U1.44 (PA11), U4.A7 (DN1), U4.B7 (DN2)
VBAT: BT1.1 (+), U1.1 (VBAT), U12.22 (V_BCKP)
VBUS: C16.1, D3.5, R5.1, R7.1, TP4.1, U4.A4B9 (VBUS), U4.B4A9 (VBUS), U7.8 (IN1)
VIN_EXT: C19.1, J1.2, J3.1, J3.2, J3.3, J3.4, J3.5, J3.6, J3.7, J3.8, R9.1, TP1.1, U7.6 (IN2)

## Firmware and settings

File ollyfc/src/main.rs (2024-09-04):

#![no_std]
#![no_main]

/// modules
use ollyfc::io;

/// configuration
use defmt_rtt as _;
use panic_probe as _;

/// system
use rtic_monotonics::systick_monotonic;
systick_monotonic!(Mono, 1000);

/// hal
use embedded_hal_bus::spi::{ExclusiveDevice, NoDelay};
use stm32f4xx_hal::prelude::*;
use stm32f4xx_hal::{dma, gpio, pac, serial, spi};
use w25q::W25Q;

/// type
type SpiFlash = W25Q<
    ExclusiveDevice<spi::Spi<pac::SPI1>, gpio::Pin<'A', 4, gpio::Output>, NoDelay>,
    stm32f4xx_hal::timer::Delay<pac::TIM2, 1000>,
>;

type RxTransfer = dma::Transfer<
    dma::Stream2<pac::DMA2>,
    4,
    serial::Rx<pac::USART1>,
    dma::PeripheralToMemory,
    &'static mut [u8; SBUS_BUFFER_SIZE],
>;

const SBUS_BUFFER_SIZE: usize = 25;

#[rtic::app(device = stm32f4xx_hal::pac, peripherals = true, dispatchers = [USART1, I2C2_ER, I2C2_EV, SPI4])]
mod app {

    use stm32f4xx_hal::serial;

    use super::*;

    #[shared]
    struct Shared {
        sbus_transfer: RxTransfer,
    }

    #[local]
    struct Local {
        _mem: SpiFlash,
        sbus_buffer: Option<&'static mut [u8; SBUS_BUFFER_SIZE]>,
    }

    #[init]
    fn init(cx: init::Context) -> (Shared, Local) {
        let dp = cx.device;
        let rcc = dp.RCC.constrain();
        let hse = 16.MHz();
        let sysclk = 64.MHz();
        let clocks = rcc
            .cfgr
            .use_hse(hse)
            .sysclk(sysclk)
            .require_pll48clk()
            .freeze();

        let _syscfg = dp.SYSCFG.constrain();
        Mono::start(cx.core.SYST, sysclk.to_Hz());

        let gpioa = dp.GPIOA.split();
        let gpiob = dp.GPIOB.split();

        // SPI Flash
        let spi1 = dp.SPI1.spi(
            (
                gpioa.pa5.into_alternate(),
                gpioa.pa6.into_alternate(),
                gpioa.pa7.into_alternate(),
            ),
            embedded_hal::spi::MODE_0,
            8.MHz(),
            &clocks,
        );
        let cs = gpioa.pa4.into_push_pull_output();
        let spidev = ExclusiveDevice::new_no_delay(spi1, cs).unwrap();
        let mem = W25Q::new_with_spi(spidev, dp.TIM2.delay_ms(&clocks));
        // SPI Flash

        // SBUS UART
        let rx_pin = gpiob.pb7.into_alternate();
        let mut rx = dp
            .USART1
            .rx(
                rx_pin,
                serial::Config::default()
                    .baudrate(100_000.bps())
                    .dma(serial::config::DmaConfig::Rx),
                &clocks,
            )
            .unwrap();
        rx.listen_idle();
        let sbus_buffer = cortex_m::singleton!(: [u8; SBUS_BUFFER_SIZE] = [0; SBUS_BUFFER_SIZE]);
        let mut sbus_transfer = dma::Transfer::init_peripheral_to_memory(
            dma::StreamsTuple::new(dp.DMA2).2,
            rx,
            cortex_m::singleton!(: [u8; SBUS_BUFFER_SIZE] = [0; SBUS_BUFFER_SIZE]).unwrap(),
            None,
            dma::config::DmaConfig::default()
                .memory_increment(true)
                .fifo_enable(true)
                .fifo_error_interrupt(true)
                .transfer_complete_interrupt(true),
        );
        sbus_transfer.start(|_rx| {});
        // SBUS UART

        (
            Shared { sbus_transfer },
            Local {
                _mem: mem,
                sbus_buffer,
            },
        )
    }

    #[task(priority=3, binds = DMA2_STREAM2, shared = [sbus_transfer], local = [sbus_buffer])]
    fn sbus_data(mut cx: sbus_data::Context) {
        cx.shared.sbus_transfer.lock(|xfer: &mut RxTransfer| {
            if xfer.is_idle() {
                let new_buf = cx.local.sbus_buffer.take().unwrap();
                let (buf, _current) = xfer.next_transfer(new_buf).unwrap();
                let chan_data = io::sbus::SbusData::new(*buf).parse();
                // free the buffer
                cx.local.sbus_buffer.replace(buf);
                match chan_task::spawn(chan_data) {
                    Ok(_) => (),
                    Err(e) => {
                        defmt::error!("Error spawning task: {:?}", e);
                        panic!();
                    }
                };
            }
        });
    }

    #[task()]
    async fn chan_task(_cx: chan_task::Context, chan_data: io::sbus::SbusChannels) {
        let inputs = chan_data.get_input();

        defmt::info!(
            "throttle: {}\t aileron: {}\t elevator: {}\t rudder: {}\t, arm: {}\t, enable: {}\t, record: {}\t",
            inputs.throttle,
            inputs.aileron,
            inputs.elevator,
            inputs.rudder,
            inputs.arm,
            inputs.enable,
            inputs.record
        );
    }
}

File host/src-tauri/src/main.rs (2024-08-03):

// Prevents additional console window on Windows in release, DO NOT REMOVE!!
#![cfg_attr(not(debug_assertions), windows_subsystem = "windows")]

use log::LevelFilter;

mod usb;

fn main() {
    tauri::Builder::default()
        .plugin(
            tauri_plugin_log::Builder::default()
                .level(LevelFilter::Debug)
                .build(),
        ) // <-- this line here
        .invoke_handler(tauri::generate_handler![
            usb::get_usb_devices,
            usb::get_selected_device,
            usb::select_device,
            usb::connect_to_device,
            usb::disconnect_device,
            usb::get_connection_status,
        ])
        .run(tauri::generate_context!())
        .expect("error while running tauri application");
}

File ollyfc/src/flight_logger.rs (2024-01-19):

use defmt::{debug, error, info};
use rtic::Mutex;
use rtic_monotonics::{systick::Systick, Monotonic};

use crate::w25q::{self, FlashMem, MemError, PAGE_SIZE};

use ollyfc_common::log::LogInfoPage;
use ollyfc_common::{FlightLogData, LOG_SIZE};

// size of the log item, in bytes
pub const LOG_PAGE_SIZE: usize = crate::w25q::PAGE_SIZE as usize;
pub const LOGS_IN_PAGE: usize = LOG_PAGE_SIZE / LOG_SIZE;
pub const INFO_SECTOR_ADDR: u32 = 0x00;

pub struct FlightLogger<T: FlashMem> {
    pub mem: T,
    addr_ptr: u32,
    block_start_ptr: u32,
    block_end_ptr: u32,
    block_size: u32,
    n_blocks: u32,
    enable: bool,
}

impl<T: FlashMem> FlightLogger<T> {
    // mem: the memory object
    // start: start address
    // nblocks: number of blocks to write starting at
    //     the start address
    // enable: whether to enable logging to mem
    pub fn new(mem: T, start: u32, nblocks: u32, enable: bool) -> Self {
        let block_count = w25q::N_BLOCKS_32K as u32;
        let block_size = w25q::BLOCK_32K_SIZE as u32;

        if start > block_count {
            panic!("Start block address out of bounds");
        } else if start < 1 {
            panic!("Start block no. must be 1 or greater");
        }
        if start + nblocks > block_count {
            panic!("End block address out of bounds");
        }

        let block_start_ptr = start * block_size;
        let addr_ptr = block_start_ptr;
        let block_end_ptr = (start + nblocks) * block_size;

        // create the object
        let mut this = Self {
            mem: mem,
            addr_ptr: addr_ptr,
            block_start_ptr: block_start_ptr,
            block_end_ptr: block_end_ptr,
            block_size: block_size,
            n_blocks: nblocks,
            enable: enable,
        };
        info!(
            "Created logger. start=0x{:x} end=0x{:x} blocksize={} nblocks={}",
            this.block_start_ptr, this.block_end_ptr, this.block_size, this.n_blocks
        );
        if enable {
            this.write_info_page();
        }

        return this;
    }

    /// info page
    pub fn write_info_page(&mut self) {
        // sector erase
        match self.mem.sector_erase(0x00) {
            Ok(_) => (),
            Err(e) => match e {
                MemError::SpiError(_) => error!("SPI error"),
                MemError::NotAlignedError => error!("Page not aligned"),
                MemError::OutOfBoundsError => error!("Data out of bounds"),
            },
        }

        let info = LogInfoPage::new(
            self.block_start_ptr,
            self.block_end_ptr,
            self.block_size,
            self.n_blocks,
            self.addr_ptr,
            PAGE_SIZE,
        );

        let mut buf = [0u8; LOG_PAGE_SIZE];

        info.to_bytes().iter().enumerate().for_each(|(i, b)| {
            buf[i] = *b;
        });

        match self.mem.page_program(0x00, &buf) {
            Ok(_) => (),
            Err(e) => log_mem_error(e),
        };
    }

    pub fn read_info_page(&mut self) -> LogInfoPage {
        let mut buf = [0u8; LOG_PAGE_SIZE];
        match self.mem.read(0x00, &mut buf) {
            Ok(_) => (),
            Err(e) => log_mem_error(e),
        }

        return LogInfoPage::from_bytes(&buf);
    }

    pub fn log(&mut self, data: &[FlightLogData; LOGS_IN_PAGE]) {
        // erase the sector ahead before writing
        if self.enable {
            if self.addr_ptr % self.mem.sector_size() as u32 == 0 {
                match self.mem.sector_erase(self.addr_ptr) {
                    Ok(_) => (),
                    Err(e) => log_mem_error(e),
                }

                // also write the address pointer
                match self.mem.sector_erase(INFO_SECTOR_ADDR) {
                    Ok(_) => (),
                    Err(e) => log_mem_error(e),
                }
                // writes the current addr ptr.
                self.write_info_page();
            }
        }
        // serialize onto a page
        let mut buf = [0u8; LOG_PAGE_SIZE];
        for (i, log) in data.iter().enumerate() {
            buf[i * LOG_SIZE..(i + 1) * LOG_SIZE].copy_from_slice(&log.to_bytes());
        }

        // write the page
        if self.enable {
            info!("Writing page at 0x{:x}", self.addr_ptr);
            match self.mem.page_program(self.addr_ptr, &buf) {
                Ok(_) => (),
                Err(e) => match e {
                    MemError::SpiError(_) => error!("SPI error"),
                    MemError::NotAlignedError => error!("Page not aligned"),
                    MemError::OutOfBoundsError => error!("Data out of bounds"),
                },
            };
        }

        // increment the address pointer
        self.incr_addr_ptr();

        // rollover
        if self.addr_ptr >= self.block_end_ptr {
            self.addr_ptr = self.block_start_ptr;
        }
    }

    fn incr_addr_ptr(&mut self) {
        self.addr_ptr += self.mem.page_size() as u32;
    }

    pub fn addr_ptr(&self) -> u32 {
        self.addr_ptr
    }
    pub fn block_start_ptr(&self) -> u32 {
        self.block_start_ptr
    }
    pub fn block_end_ptr(&self) -> u32 {
        self.block_end_ptr
    }
    pub fn n_blocks(&self) -> u32 {
        self.n_blocks
    }
    pub fn erase_block(&mut self, block: u32) {
        let address = self.block_start_ptr + block * self.block_size;
        info!(
            "Erasing block {} of {} at 0x{:x} to 0x{:x}",
            block,
            self.n_blocks,
            address,
            address + self.block_size
        );
        match self.mem.block64_erase(address) {
            Ok(_) => (),
            Err(e) => log_mem_error(e),
        };
    }
}

/// Log a memory error
fn log_mem_error(e: crate::w25q::MemError<stm32f4xx_hal::spi::Error>) {
    match e {
        MemError::SpiError(_) => error!("SPI error"),
        MemError::NotAlignedError => error!("Page not aligned"),
        MemError::OutOfBoundsError => error!("Data out of bounds"),
    }
}
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

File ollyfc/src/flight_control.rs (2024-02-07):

use defmt::info;
use rtic::Mutex;
use rtic_monotonics::{
    systick::{ExtU32, Systick},
    Monotonic,
};

use ollyfc_common::{ControlPolicy, FlightLogData, SBusInput, SensorInput};

#[derive(Debug, Clone, Copy, PartialEq, defmt::Format)]
enum SwitchMode {
    Low,
    Neutral,
    High,
}

fn switch_mode(switch_input: u16) -> SwitchMode {
    if switch_input < 500 {
        SwitchMode::High
    } else if switch_input > 1500 {
        SwitchMode::Low
    } else {
        SwitchMode::Neutral
    }
}

fn elevator_ctl(ele: u16, en: SwitchMode) -> u16 {
    if en == SwitchMode::High {
        ele + 200
    } else {
        ele
    }
}

fn aileron_ctl(ail: u16) -> u16 {
    ail
}

fn rudder_ctl(rud: u16) -> u16 {
    rud
}

fn throttle_ctl(thr: u16) -> u16 {
    thr
}

fn scale_servo(elevator: u16, duty_max: u16) -> u16 {
    let min_pulse_width = 900; // 900 μs
    let max_pulse_width = 2100; // 2100 μs
    let pulse_width_range = max_pulse_width - min_pulse_width;
    let servo_pulse_width =
        min_pulse_width + (elevator as f32 / 2048.0 * pulse_width_range as f32) as u16;
    let pwm_duty = (servo_pulse_width as f32 / 20000.0 * duty_max as f32) as u16;
    return pwm_duty;
}

pub async fn flight_loop(
    mut cx: crate::app::primary_flight_loop_task::Context<'_>,
    mut log_ch_s: rtic_sync::channel::Sender<'static, FlightLogData, { crate::LOGDATA_CHAN_SIZE }>,
) {
    loop {
        let now = rtic_monotonics::systick::Systick::now();
        // Flight Controls
        let controls = cx
            .shared
            .flight_controls
            .lock(|fc: &mut crate::sbus::FlightControls| fc.clone());
        let arm_mode = switch_mode(controls.arm);
        let enable_mode = switch_mode(controls.enable);
        let record_mode = switch_mode(controls.record);

        info!(
            "rec: {}, arm: {}, en: {}",
            record_mode, arm_mode, enable_mode
        );
        // Sensor
        let gyro = cx.shared.sensor.lock(|g: &mut SensorInput| g.clone());
        #[cfg(feature = "no-sensors")]
        let gyro = SensorInput::default();

        // control policies
        let ele = elevator_ctl(controls.elevator, arm_mode);
        let ail = aileron_ctl(controls.aileron);
        let rud = rudder_ctl(controls.rudder);
        let thr = throttle_ctl(controls.throttle);

        // Send data to logger
        let log_data = FlightLogData {
            timestamp: Systick::now().ticks(),
            sbus_input: SBusInput {
                throttle: controls.throttle,
                aileron: controls.aileron,
                elevator: controls.elevator,
                rudder: controls.rudder,
                arm: arm_mode as u16,
                enable: enable_mode as u16,
                record: record_mode as u16,
            },
            sensor_input: SensorInput {
                pitch: gyro.pitch,
                yaw: gyro.yaw,
                roll: gyro.roll,
                accel_x: gyro.accel_x,
                accel_y: gyro.accel_y,
                accel_z: gyro.accel_z,
            },
            control_policy: ControlPolicy {
                ctl_elevator: ele,
                ctl_aileron: ail,
                ctl_rudder: rud,
                ctl_throttle: thr,
            },
        };
        if record_mode == SwitchMode::High {
            info!("Sending log data");
        }
        log_ch_s
            .send(log_data)
            .await
            .expect("Error sending log data");

        let duty = scale_servo(ele, cx.local.elevator_channel.get_max_duty());
        cx.local.elevator_channel.set_duty(duty);

        rtic_monotonics::systick::Systick::delay_until(now + 20u32.millis()).await;
    }
}

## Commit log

2023-12-09 flash storage driver and rtic main
2023-12-09 fix compile issues with w25q
    [w25q.rs]
2023-12-09 Flight logger
    The flight logger is designed to consume sensor and registered flight
    control inputs and write them to the built-in spi flash. The logging
    system is composed of two tasks: a log collector task and a log writer
    task. The log collector collects log entries at a regular interval and
    adds them to a queue. The log writer task consumes the queue, packs the
    entries (32 bytes) into a flash page (256 bytes), and writes the page
    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
2023-12-09 MPU6050 sensor
    Add task to handle storing of MPU6050 sensor data. Updated flight data
    type to be 64 bytes (up from 32 bytes) since we have 6 x 4 byte floats
    for accel x, y, z and gyro x, y, z.
2023-12-09 Added interrupt for sensor task.
    Sensor task will now be triggered whenvever sensor recieves new data
    (1kHz).
2023-12-09 Fix interrupts for gyroscope
    [main.rs]
2023-12-09 sbus read over DMA
2023-12-09 PWM, flight control module, and some reorg of
    - created a new module, flight_control, that will hold control code.
    - renamed flightlogger to flight_logger
    - added PWM module for control surfaces
    - changed hardware of w25q
    - removed some timers that were not used for anything
2023-12-09 Encapsulate gyro setup logic
2023-12-09 i2c2->i2c1 for mpu6050
2023-12-10 USB configuration #3 #2
    Brought USB configuration into the program. We added a button at A0 that
    controls what mode the system is in. If the button is pressed (grounded)
    then the system boots into USB mode. Otherwise, it boots into flight
    control mode.
    The USB device and serial device is instantiated no matter what, but if
    it sits idle this doesn't impact performance and makes it significantly
    easier from an architecture standpoint.
    [main.rs]
2023-12-10 Boot mode switch
2023-12-11 WIP Svelte application for host controller #16
    Partially implemented host application. Embedded USB driver. USB task for
    listening for data from host. Host side USB enumeration and search for matching
    FC device (by VID/PID). Hardcoded VID/PID used from pid.codes. Serial control on
    host and embedded side. Verified sending commands from host to embedded, but no
    bidirectional communication yet.
2023-12-12 End-to-end IO #16
    It's still REALLY buggy and very slow.
    [flight_logger.rs, main.rs, usb.rs]
2023-12-13 Flight logs attach timestamp
2023-12-14 fix log info page buffer size issue
    [log.rs]
2023-12-26 device IO display changes
2023-12-26 Created abstraction for protocol #28
    We are going to handle most/(maybe all?) USB serial writes through a
    protocol that will CRC and ack the data. This makes it more ergonomic
    (abstract the HAL calls) and more reliable (CRC). For details see the
    issue.
    [flight_control.rs, main.rs, usb.rs]
2023-12-27 Log read sequence
    Implemented log read sequence for host application. Sending the log read command to the device enters a special mode, "direct access", where we can read a page from the flash. We get the address boun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
2023-12-28 Fixed compilation warnings.
    I needed to create a no_sensors feature so that the board would boot when disconnected from the external peripherals (the Rx and the gyro). Fixed the issues I was having with those peripherals so it's not needed anymore.
    [flight_control.rs, log.rs, main.rs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]
2024-02-07 BMI160 sensor
2024-02-07 PCB KiCad Project. Schematics, board files, BOM
    [bom.csv, designators.csv, ollyfc.kicad_pcb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]
2024-02-11 some hardware designs
    [NEO-M9N-00B.step, bom.csv, designators.csv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]
2024-02-14 Route another?
    [ollyfc.kicad_pcb, ollyfc.kicad_sch, power.kicad_sch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]
2024-02-18 v2 PCB design
    [ollyfc.kicad_pcb, ollyfc.kicad_sch, sensor.kicad_sch]
2024-02-25 JLC part footprints
    [ollyfc.kicad_pcb, ollyfc.kicad_sch, power.kicad_sch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]
2024-03-09 v2 files
    [NEO-M9N-00B.step, bom.csv, designators.csv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]
2024-03-10 Update BMP388 dependency to use new driver
2024-03-10 New shared library
    The way I'm thinking we do this is that all of the application logic
    will be in a library that can be shared across multiple different
    hardware applications. Individual BBU tasks will be in "examples" that
    are able to be developed independently. So, starting with the pressure
    sensor, we have an example code that called bbu-bmp388.rs that will
    exercise all possible functions of the pressure sensor. Successful BBU
    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
2024-03-10 #35 Bring-up example for pressure sensor
2024-03-10 #35 bmp388 fix, clear interrupt on sensor side after read
2024-03-10 #39 lis3mdl sensor read in ISR
2024-03-27 #36 Fix short in PCA9865, Remove 'TP' silkscreens
    [sensor.kicad_sch]
2024-03-27 Re-organize test points. Fix LED footprints #36
    [ollyfc.kicad_sch, power.kicad_sch, sensor.kicad_sch]
2024-03-27 Add aux line #36
    [ollyfc.kicad_sch]
2024-03-27 remove unused in pressure.rs
2024-03-27 STM32F411 SVD
2024-04-02 v3 schematic + layout
    [ollyfc.kicad_sch, sensor.kicad_sch]
2024-04-02 Added some organization to schematic
    [ollyfc.kicad_sch, power.kicad_sch, sensor.kicad_sch]
2024-04-10 dead-end board files
    [ollyfc.kicad_sch, sensor.kicad_sch]
2024-04-10 add v3 board redesign
    [bom.csv, designators.csv, io.kicad_sch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]
2024-04-17 Update board configuration
2024-04-21 PWM - LED and Servo control
2024-04-30 imu bring-up with interrupt config
2024-04-30 pwm bring-up example changes
2024-07-26 add board schematic PDF for easy reference
2024-08-01 - common Message type with cross platform CRC - usb (firmware) configured as bulk transfer device - fixes to ollyfc_common which make it more readable for conditionally compiled parts - addition of .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
    [log.rs, usb.rs]
2024-08-04 emphasis for compatible device in USB list
2024-08-04 fix compiler warnings in imu example
    [imu.rs, mod.rs]
2024-08-05 status LED
2024-08-05 pin stm32f4xx-hal
2024-08-05 update pressure sensor example to show altitude
2024-08-05 added some tone definitions to buzzer example
    [buzzer.rs]
2024-08-05 i2c test code for checking the i2c3 bus
2024-09-04 Fix warnings across the project, clean up lib
    [bmp388.rs, buzzer.rs, hdc-1080.rs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]
